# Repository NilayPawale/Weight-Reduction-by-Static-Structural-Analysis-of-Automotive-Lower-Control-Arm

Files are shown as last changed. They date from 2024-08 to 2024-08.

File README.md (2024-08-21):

# Weight-Reduction-by-Static-Structural-Analysis-of-Automotive-Lower-Control-Arm

The control arm is a unique type of independent suspension used in automobile vehicles. 
During the actual working condition, the maximum load is transferred from upper arm to 
the A arm which creates possibility of failure in the arm. Hence it is essential to focus on 
the stress analysis of A control arm to improve and modify the existing design. A control 
arm is an important part used in a suspension system of a car. control arm performance a 
major role in managing the motion of the wheel during bump, turning, and breaking. This 
paper proposed the design optimization and model analysis of steel cast for the front A 
control arm was investigated. CATIA software was utilized to design the A control arm. 
ANSYS 19 software was also used to analyze the structural strength and optimize the parts 
weight. The target of the new design was a 20% weight reduction from the existing part 
fabricated using steel material. Testing and validation of new design using FFT analysis. 
Model analysis carried out to find out natural frequencies of A control arm and validation 
are done with the help of FFT analyzer and Impact Hammer Test. 

The lower control arm gets more attention by many researches like study dynamic analyses 
of the motor vehicle suspension system using the point-joint coordinate’s formulation. The 
mechanical system is replaced by an equivalent constrained system of particles and then 
the laws of particle dynamics are used to derive the equations of motion. Modelling and 
simulation are indispensable when dealing with complex engineering systems. It makes it 
possible to do an essential assessment before systems are developed. It can provide support 
in all stages of a project from conceptual design, through commissioning and operation. 
The most effective was to improve product quality and reliability is to integrate them in 
the design and manufacturing process. 

## Significance of Project 

The suspension system caries the vehicle body and transmit all forces between the body 
and the road without transmitting to the driver and passengers. The suspension system of a 
car is used to support its weight during varying road conditions. The suspension system is 
made of several parts and components. These include the front and rear. The suspension 
arm gets more attention by many researches like study dynamic analyses of the motor 
vehicle suspension system using the point-joint coordinate’s formulation. Modeling and 
simulation are indispensable when dealing with complex engineering systems. It can 
provide support in all stages of a project from conceptual design, through commissioning 
and operation. The most effective way to improve product quality and reliability is to 
integrate them in the design and manufacturing process. 

## Objectives

1. To prepare CAD design using CATIA V5. 
2. Static structural Analysis of Automotive A type control arm 
3. Optimization of Automotive A type control arm. 
4. To perform static structural analysis of the suspension arm using ANSYS Software. 
5. To optimize the lower control arm for weight reduction” (unsprung weight) up to 
5-20% and suggest alternate design. 
6. Testing and validation of Automotive A type control arm with the help of 
Universal Testing Machine. 
7. To compare the factor of safety for optimized and baseline design of lower 
control arm by keeping factor of safety for optimized design within permissible 
limits. 
8. To perform experimentation on physical model of Lower Control Arm.

## Softwares Used: 
Catia, SolidWorks, Ansys

## Results obtained from the project

### Elements Details of Ansys -  
- Nodes – 28547 for Existing component and 27382 for Optimized component. 
- Elements - 14197 for Existing component and 13451 for Optimized component. 

### Universal Testing Machine Results -  
- The Deformation Maximum is 2.593mm for Existing component and 2.869 mm 
for Optimized component. 
- The Deformation Minimum is 0mm for Existing component and 0mm for 
Optimized component. 
- The Von-mises stress Maximum are 350.22 MPA for Existing component and 
399 MPA for Optimized component. 
- The Von-mises stress Minimum are 0.0012 MPa for Existing component and 
0.0014 MPA for Optimized component. 
- Mass of the Existing component is 2.55 KG for Existing component and 2.39 KG 
(6.07% weight reduction) for Optimized component. 
- Factor of Safety of the Existing component is 1.31 for existing component and 
1.15 for Optimized component. 

The existing design has been modified, by reducing the thickness of the existing profile. 
The optimization of lower control arm is done by applying the Design of Experiments 
method. The parameters are identified. The FEA is done on LCA and the buckling load 
has been compared with the existing component. The sheet metal thickness of the new 
design has been reduced from 3.6 mm to 3mm. For the mass production the cost has been 
reduced to Rs.34000 for 2000 products in a batch as assumed. For the modified design 
the structural rigidity has been increased for the LCA, when compared to the existing 
design. Finally, mass of the control arm has been reduced up to 6.07 % when compared 
with existing model.

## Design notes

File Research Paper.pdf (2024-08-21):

# Weight Reduction by Static Structural Analysis of Automotive Lower Control Arm

Aniruddha Jadhav#1, Nilay Pawale *2, Atharva Kalokhe #3

### , Aditya Bangale #4

#Department of Mechanical Engineering, Smt Kashibai Navale College of Engineering, Savitribai Phule Pune University, Pune 1Aniruddhaj7727@gmail.com

2nilaypawale.skncoe.mech@gmail.com 3atharvkalokhe05@gmail.com 4bangale.adi@gmail.com
Abstract—
The lower control arm is a unique type of independent suspension used in automobile vehicles. During the actual working condition, the maximum load is transferred from upper arm to the A arm which creates possibility of failure in the arm. Hence it is essential to focus on the stress analysis of A suspension arm to improve and modify the existing design. A suspension arm is an important part used in a suspension system of a car. suspension arm performance a major role in managing the motion of the wheel during bump, turning, and breaking. This research proposed the design optimization and static analysis of steel cast for the front A suspension arm was investigated. CATIA software was utilized to design the A suspension arm. ANSYS 19 software was also used for analyze the structural strength and optimize the parts weight. The target of the new design was a 20% weight reduction from the existing part fabricated using steel material. Testing and validation of new design using strain gauge analysis.
Keywords— Lower Control Arm, Suspension System, Weight Reduction, Ansys, Catia
I. INTRODUCTION

The control arm is a unique type of independent suspension used in automobile vehicles. During the actual working condition, the maximum load is transferred from upper arm to the A arm which creates possibility of failure in the arm. Hence it is essential to focus on the stress analysis of A control arm to improve and modify the existing design. A control arm is an important part used in a suspension system of a car. control arm performance a major role in managing the motion of the wheel during bump, turning, and breaking. This paper proposed the design optimization and model analysis of steel cast for the front A control arm was investigated. CATIA software was utilized to design the A control arm. ANSYS 19 software was also used to analyse the structural strength and optimize the parts weight. The target of the new design was a 20% weight reduction from the existing part fabricated using steel material.
In automotive suspension, a control arm, also known as an A-arm, is a hinged suspension link between the chassis and the suspension upright or hub that carries the wheel. In simple terms, it governs a wheel's vertical travel, allowing it to move up or down when driving over bumps, into potholes, or otherwise reacting to the irregularities of a road surface. Most control arms form the lower link of a suspension.

The challenge for automotive manufacturer to produce the lightweight components but at the same time need to maintain the performance of the components. To produce the lightweight components, the main criteria to overlook are the advance material and the manufacturing technology.
Weight reduction enables the manufacturer to develop the same vehicle. If all the components in vehicle can contributed for about 10% to 20% of weight reduction, it is estimated that 20% of vehicle weight reduction results in 8–10% of fuel economy improvement. There several ways to achieve the lightweight components in vehicle. Changing a new lightweight material such as composites and aluminium alloy can give a good weight reduction to vehicle and improve the fuel economy [1].

II. LITERATURE REVIEW

Vehicles ranging from bullock carts to modern vehicles use suspension system such as, leaf springs, pneumatic and hydraulic systems. The main aim of using a suspension system is to prevent the shocks reaching the body of the vehicle from the rough roads and ensure that the vehicle’s wheels remain in contact with the road. There are two types of forces acting on the suspension system of a vehicle, the first is the force from the road disturbance, and the second is the load disturbance. Road unevenness could be of high magnitude and low frequency (such as mountains) and the small magnitude and large frequency (because of rough roads). Load disturbance includes the forces induced by the changing acceleration, braking and cornering. A suspension system should respond very smoothly against road disturbances and should be robust against load disturbances.[2]
In suspension system, the control arm is very important component. The double wishbone suspension system contains lower control arm and upper control arm. The McPherson structural suspension system contains only lower control arm. Between wheel assembly and vehicle chassis the control arms are rigidly placed.
The control arm is connected to the chassis with the help of bush which is placed in pivot joints. Rear and front bushes are used in control arms. it has U-shaped configuration. At the apex of the control arm a ball joint receptacle is formed.[3]

The ball joint receptacle is adapted to cooperate with a ball joint assembly and may include a ball joint housing integrally formed with the control arm. Typical modern control arm incorporates a separate ball joint housing which is inserted in to the apex of control arm. The bushing apertures are designed to retain pipe housings for mating engagement with a pivot bar assembly forming a portion of the vehicle suspension system.[3]

III. PROBLEM DEFINITION AND OBJECTIVES

Chassis parts are a critical part of a vehicle, leaving no room for error in the design and quality the present process relates to a computer-aided structure analysis and design graphic display device and method, and more particularly, to a computer-aided structure analysis of A control arm and which is analyzed and designed, thereby meet the customer requirements of LCA.

Objectives:
1. To prepare CAD design using CATIA V5.

### 2. Static structural Analysis of Automotive A type control arm

3. Optimization of Automotive A type control arm.
4. To perform static structural analysis of the suspension arm using ANSYS Software.
5. To optimize the lower control arm for weight reduction” (unsprung weight) up to 5-20% and suggest alternate design.
6. To compare the factor of safety for optimized and baseline design of lower control arm by keeping factor of safety for optimized design within permissible limits.
7. To perform experimentation on physical model of Lower Control Arm.

IV.METHODOLOGY
The methodology of our project would be starting with the topic selection, then working on the topic by researching and creating a detailed plan for execution of the project. Then executing the project by manufacturing and then testing the model of the project. Then at last finishing the miscellaneous work and concluding the Project.

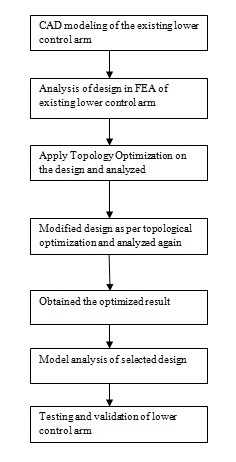
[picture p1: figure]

V. DESIGN OF LOWER CONTROL ARM

The finite element method (FEM), is a numerical method for solving problems of engineering and mathematical physics. Typical problem areas of interest include structural analysis, heat transfer, fluid flow, mass transport, and electromagnetic potential. The analytical solution of these problems generally requires the solution to boundary value problems for partial differential equations. The finite element method formulation of the problem results in a system of algebraic equations. The method yields approximate values of the unknowns at discrete number of points over the domain. To solve the problem, it subdivides a large problem into smaller, simpler parts that are called finite elements.

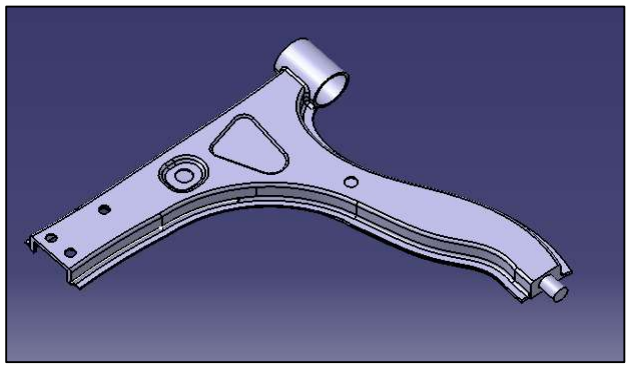
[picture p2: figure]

Lower Control Arm CAD

In present research for analysis ANSYS (Analysis System) software is used. Basically, its present FEM method to solve any problem. Following are steps in detail

### 1. Geometry 2. Discretization (Meshing) 3. Boundary condition 4. Solve (Solution) 5. Interpretation of results

Step 1: Details of material namely copper, steel, grey cast iron, composite material, fluid domain material is defined in engineering data. i.e., ANSYS default material is structural steel.
Step 2: Import of geometry created in any CAD software namely CATIA, PRO E, SOLIDWORK, INVENTOR etc. in geometry section. If any correction is to be made it can be created in geometry section in Design modeller or space claim.
Step 3: In model section after import of component
- Material is assigned to component as per existing material
- Connection is checked in contact region i.e., bonded, frictionless, frictional, no separation etc. for multi body components.
- Meshing or discretization is performed i.e., to break components in small pieces (elements) as per size i.e., preferably tetra mesh and hexahedral mesh for 3D geometry and for 2 D quad or trial are generally preferred.
Step 4: Boundary condition are applied as per analysis namely in fixed support, pressure, force, displacement, velocity as per condition.
Step 5: Now problem is well defined and solve option is selected to obtain the solution in the form of equivalent stress, strain, energy, reaction force etc.
Table 1. Material properties

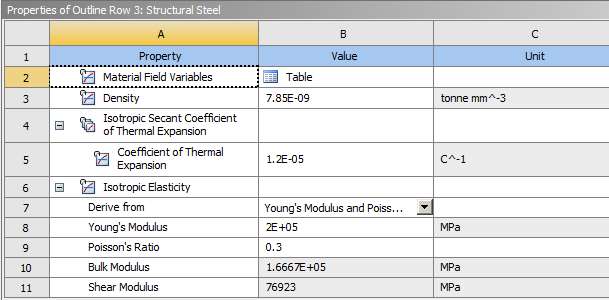
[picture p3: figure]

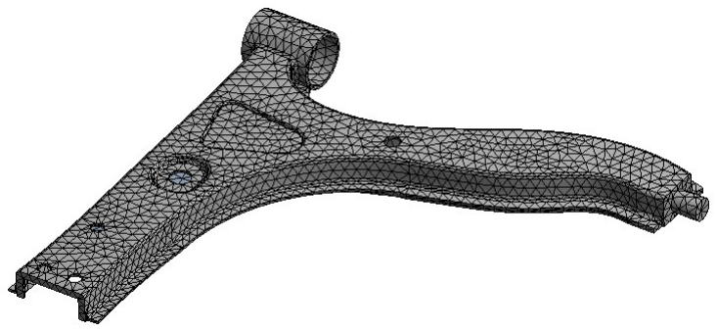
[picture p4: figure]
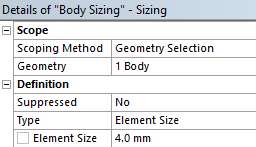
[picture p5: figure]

Fig 1. Meshing of model

Fig 2. Elements Details

A. Boundary Condition

A boundary condition for the model is the setting of a known value for a displacement or an associated load. For a particular node you can set either the load or the displacement but not both.
The main types of loading available in FEA include force, pressure and temperature. These can be applied to points, surfaces, edges, nodes and elements or remotely offset from a feature. The way that the model is constrained can significantly affect the results and requires special consideration. Over or under constrained models can give stress that is so inaccurate that it is worthless to the engineer. In an ideal world we could have massive assemblies of components all connected to each other with contact elements but this is beyond the budget and resource of most people. We can however, use the computing hardware we have available to its full potential and this means understanding how to apply realistic boundary conditions.

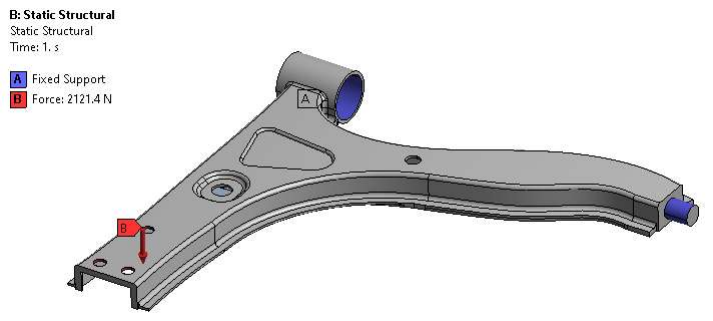
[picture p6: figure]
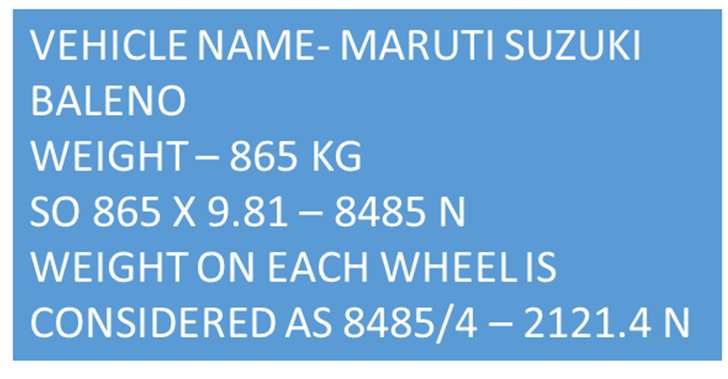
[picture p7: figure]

Fig 3. Boundary condition of model

B. Total Deformation

The total deformation & directional deformation are general terms in finite element methods irrespective of software being used. Directional deformation can be put as the displacement of the system in a particular axis or user defined direction. Total deformation is the vectors sum all directional displacements of the systems.

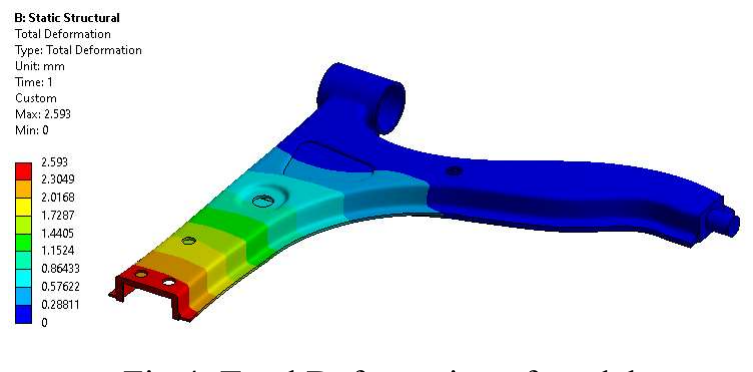
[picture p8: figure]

Fig 4. Total Deformation of model

C. Steps in Topology Optimization

The topology optimization consists of the following sequence of steps.
- Define the design space
- Define optimization parameters
- Material removal process and detail design
Step 1: Details of material namely copper, steel, grey cast iron, composite material, fluid domain material is defined in engineering data. i.e., ANSYS default material is structural steel.
Step 2: Import of geometry created in any CAD software namely CATIA, PRO E, SOLIDWORK, INVENTOR etc. in geometry section. If any correction is to be made it can be created in geometry section in Design modeller or space claim.
Step 3: In model section after import of component
- Material is assigned to component as per existing material
- Connection is checked in contact region i.e., bonded, frictionless, frictional, no separation etc. for multi body components.
- Meshing or discretization is performed i.e., to break components in small pieces (elements) as per size i.e., preferably tetra mesh and hexahedral mesh for 3D geometry and for 2 D quad or trial are generally preferred.
Step 4: Boundary condition are applied as per analysis namely in fixed support, pressure, force, displacement, velocity as per condition.
Step 5: Now problem is well defined and solve option is selected to obtain the solution in the form of equivalent stress, strain, energy, reaction force etc.
Step 6: Topology optimization tool is selected from ANSYS list view and drag and dropped in solution section of static structural so that it takes its all-boundary condition, geometry, all details and perform topology optimization on selected component.
Step 7: Define the topology density and element density section as output. After performing topology algorithm on component, selected parts contain red, brown and grey colour on it. So, red region colour indicates material removal area along with marginal (brown colour) and grey colour to keep material.
Step 8: After selection of specific shape material is removed from component and reanalysis of component is performed to observe the sustainability of existing optimized component under same boundary condition.

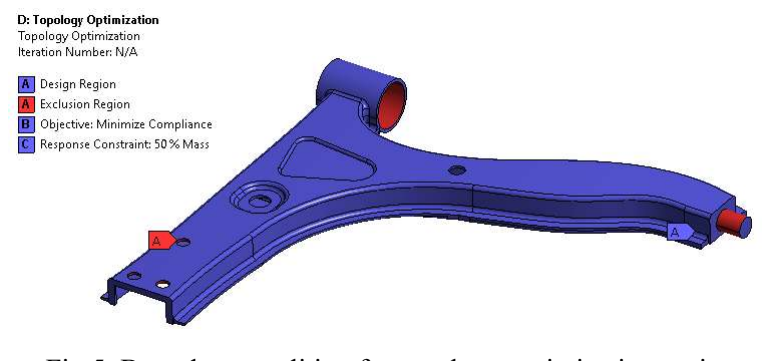
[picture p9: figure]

Fig 5. Boundary condition for topology optimization region

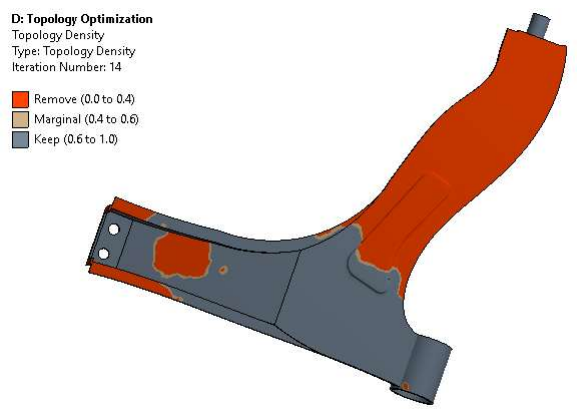
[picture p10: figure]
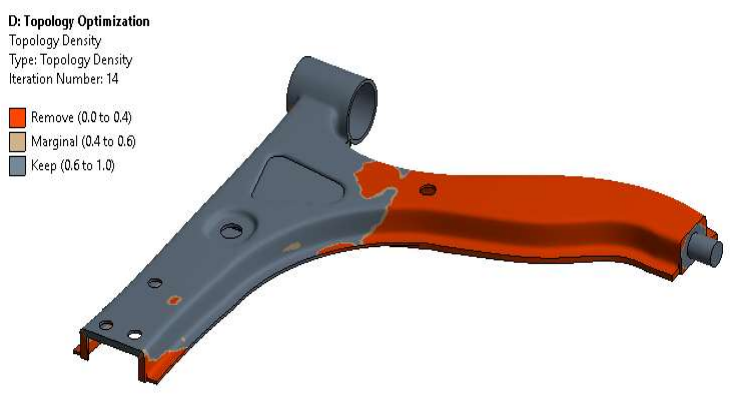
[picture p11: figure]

Fig 6. Topology optimized results

- Red region indicates material removal area region.

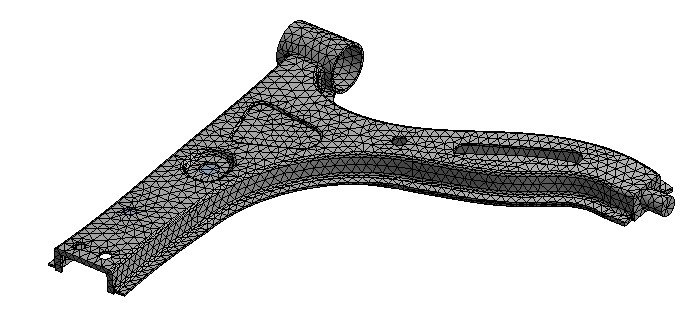
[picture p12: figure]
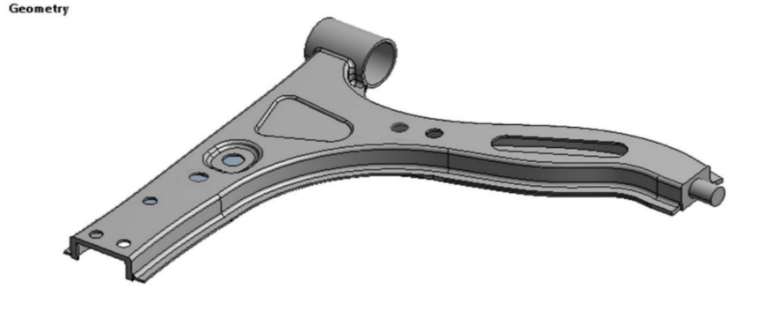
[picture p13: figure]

Fig 7. Optimized lower control arm

Fig 8. Details of optimized lower control arm

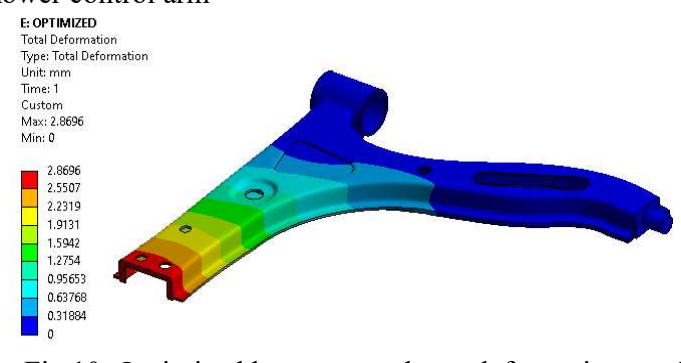
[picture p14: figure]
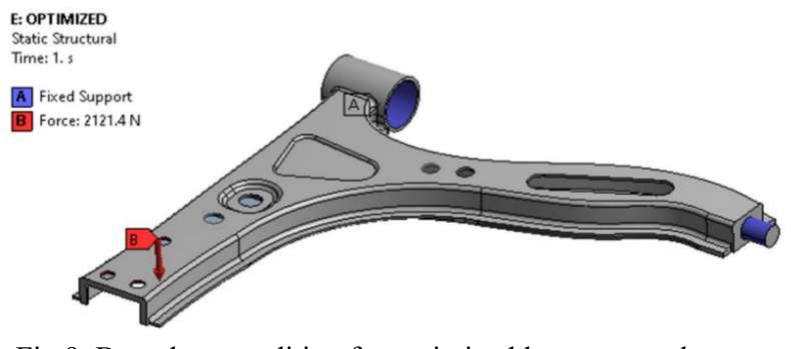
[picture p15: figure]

Fig 9. Boundary condition for optimized lower control arm | Fig 10. Optimized lower control arm deformation result

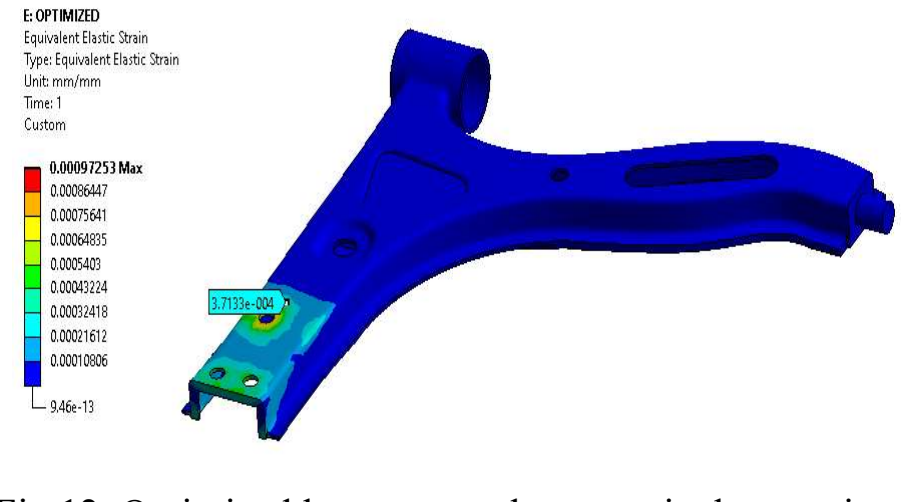
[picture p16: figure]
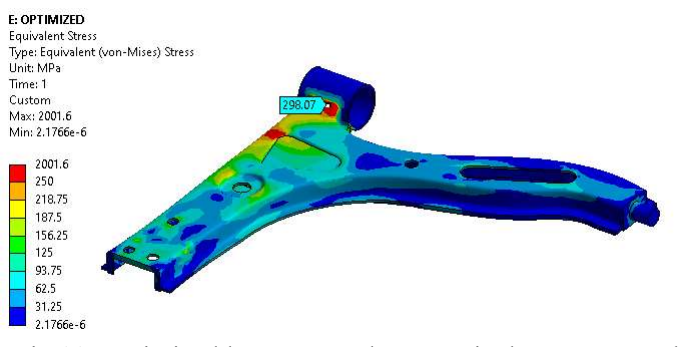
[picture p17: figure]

Fig 11. Optimized lower control arm equivalent stress result | Fig 12. Optimized lower control arm equivalent strain result
- Strain is observed around 371 microns.

VI.EXPERIMENTAL TEST

A Universal Testing Machine (UTM) is used to test both the tensile and compressive strength of materials. Universal Testing Machines are named as such because they can perform many different varieties of tests on an equally diverse range of materials, components, and structures.
Universal Testing Machines can accommodate many kinds of materials, ranging from hard samples, such as metals and concrete, to flexible samples, such as rubber and textiles. This diversity makes the Universal Testing Machine equally applicable to virtually any manufacturing industry.

TABLE 2 -SPECIFICATION OF UTM

1 | Max Capacity | 400KN
2 | Measuring range | 0-400KN
3 | Least Count | 0.04KN
4 | Clearance for Tensile Test | 50-700 mm
5 | Clearance for Compression Test | 0- 700 mm
6 | Clearance Between column | 500 mm
7 | Ram stroke | 200 mm
8 | Power supply | 3 Phase, 440Volts, 50 cycle. A.C
9 Overall dimension of machine | (L*W*H) | 2100*800*2060
10 | Weight | 2300Kg

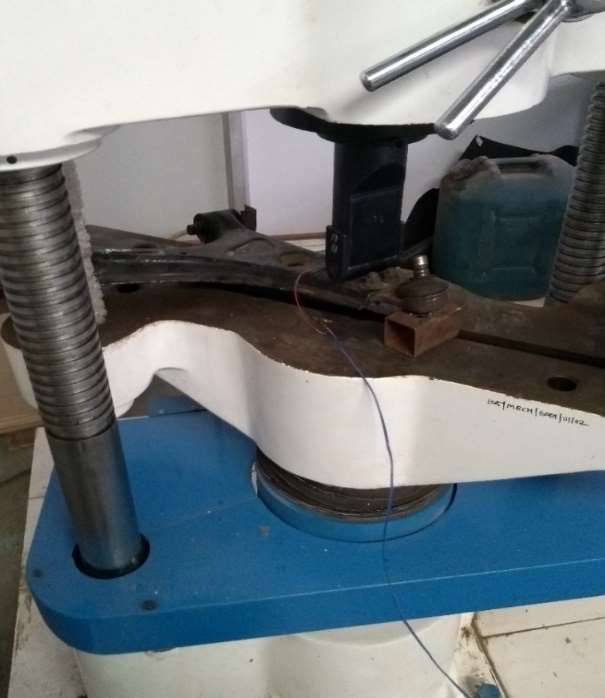
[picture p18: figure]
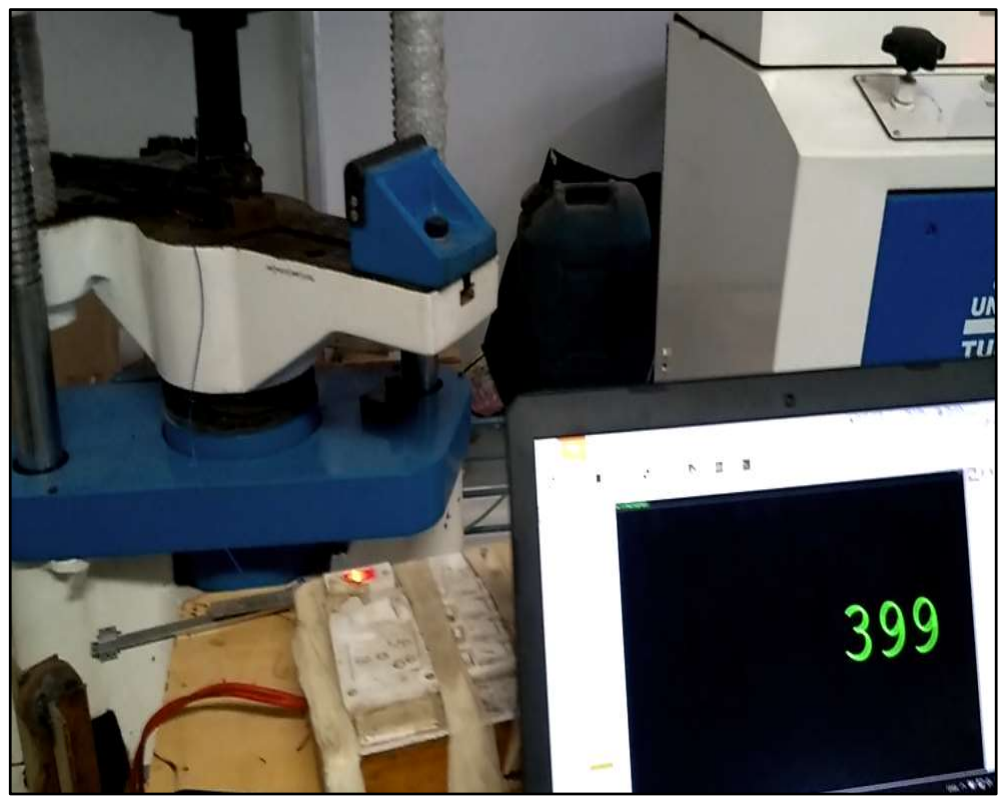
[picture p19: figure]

Fig 13. Testing in Universal Testing Machine | Fig 14. Experimental testing results

TABLE 3 - Evaluation of Results

S. No | Parameters | Existing component | Optimized component
d1 | Deformation (mm) | Max | 2.593mm | 2.869 mm
| | Min | 0 mm | 0 mm
2 Von-mises stress | (Mpa) | Max | 350.22 Mpa | 399 Mpa
| | Min | 0.0012 MPa | 0.0014 MPa
3 | Mass reduction | | 2.55 | 2.39 | 6.07% weight reduction
4 | Factor of Safety | 1.31 | | 1.15

VII. SCOPE OF FUTURE WORK

This project can be extended to satisfy the following requirements as the key objectives:
- Implementing new design changes in the existing model can be done
- Identifying more materials for the proposed design and new design
- Increasing the number of levels of the response
- Based on observations design improvements will be made in terms of shape, size and material based on design modification objectives.
- The study will focus on existing design performance, advantage and limitations.

VIII.CONCLUSION

As deflection and stress of modified Lower Control Arm is within the range. Thus, the modified design is safe. Weight of the final optimized model is 2.39 kg. The total reduction in mass is observed 6.07% by keeping Factor of safety for optimized design within permissible limits.
Thus, the objective of weight reduction of unsprung mass and cost reduction has been achieved.

ACKNOWLEDGEMENT

We take this opportunity to thank all those who have contributed to successful completion of this research work. We
would like to express our sincere thanks to our guide Prof. R. N. Khachane who has encouraged us to work on this topic and also provided valuable guidance wherever required. We also extend our gratitude to Prof. T. S. Sargar (H.O.D
Mechanical Department) who have provided facilities to explore the subject with more enthusiasm.
We express our immense pleasure and thankfulness to all the teachers and staff of the Department of Mechanical Engineering of Shrimati Kashibai Navale College of Engineering for their co-operation and support.

REFERENCES

[1] Introduction of Design and Optimization of Front Lower Control Arm (FLCA) for C-Segment Passenger Car Mohd Hafizi Abdul Rahman, Mohd Shukor Salleh, Mohd Suffian Ab. Razak, Mohamad Ridzuan Mohamad Kamal, Zolkarnain Marjom, Liza Anuar and Nur Adzly Mohamad Saad
[2] Design and analysis of lower control arm of suspension system, M. Sadiq A. Pachapuri, Ravi G. Lingannavar, Nagaraj K. Kelageri, Kritesh K. Phadate Department of Mechanical Engineering, KLE Dr. M. S. Sheshgiri College of Engineering and Technology, Belagavi 590008, India
[3] COMPARISION STUDY OF LOWER CONTROL ARM WITH DIFFERENT MATERIAL, by Gururaj Dhanu and Prof. R.S.Kattimani M.Tech (Machine Design), B.L.D.E. A’s V. P. Dr.P.G.H College of Engineering and Technology, Vijayapur, Karnataka, India, Professor, Dept. of Mechanical Engineering, B.L.D.E. A’s V. P. Dr.P.G.H College of Engineering and Tehnology, Vijayapur, Karnataka, India
[4] Structural optimization of control arm for weight reduction and improved performance by Mohd Viqaruddina, D.Ramana Reddy

[5] Design and Optimization of Front Lower Control Arm (FLCA) for C-Segment Passenger Car Mohd Hafizi Abdul Rahman, Mohd Shukor Salleh, Mohd Suffian Ab. Razak, Mohamad Ridzuan Mohamad Kamal, Zolkarnain Marjom, Liza Anuar and Nur Adzly Mohamad Saad
[6] A new design optimization of light weight front lower control arm, M.H.A. Rahman, M.S. Salleh, A. Abdullah, S.H. Yahaya, M.S.A. Razak, M.R.M. Kamal, Z. Marjom, L. Anuar and N.A.M. Saad, Journal of Advanced Manufacturing Technology (JAMT), ISSN: 1985-3157 Vol. 12 No. 1 January - June 2018.
[7] Analysis and Optimization of Lower Control Arm, Kale AR, Tadamalle AP and Patil ND, crimnson publishers, evolution in mechanical engineering, ISSN: 2640-9690, August 07, 2018
[8] Design Optimization of a Lower Control Arm of Suspension System in a LCV by using Topological Approach, Swapnil S. Khode, Prof. Amol N. Patil, Prof. Amol B. Gaikwad, International Journal of Innovative Research in Science, Engineering and Technology Vol. 6, Issue 6, June 2017
[9] Optimization of the lower arm of a vehicle suspension system for road noise reduction by sensitivity analysis, Yong-Dae Kim, Jae-Eun Jeong , Jin-Su Park , In-Hyung Yang , Tae-Sang Park , Pauziah Binti Muhamad , Dong-Hoon Choi , Jae-Eung Oh, Mechanism and Machine Theory 69 (2013) 278–302
[10] Topology Optimization and Performance Calculation for Control Arms of a Suspension Liang Tang, JieWu, Jinhao Liu, Cuicui Jiang, andWen-Bin Shangguan, Hindawi Publishing Corporation Advances in Mechanical Engineering, Volume 2014, Article ID 734568

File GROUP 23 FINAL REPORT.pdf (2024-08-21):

Savitribai Phule Pune University, Pune 2019 Course

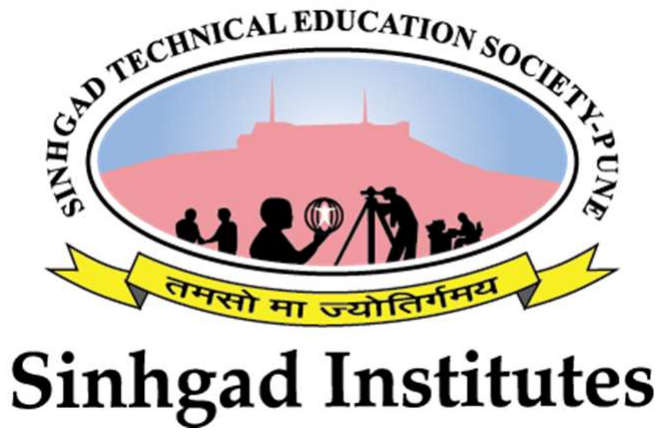
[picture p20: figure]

Smt. Kashibai Navale College of Engineering, Pune | B.E. (Mechanical Engineering)

### A Project Stage-II Report on

# Weight Reduction by Static Structural Analysis of Automotive Lower Control Arm

By

Mr. Aniruddha Jadhav | Exam. Seat No – B190360969
Mr. Nilay Pawale | Exam. Seat No – B190361088
Mr. Atharva Kalokhe | Exam. Seat No – B190360992
Mr. Aditya Bangale | Exam. Seat No – B190360828

### Guide Prof. R.N. Khachane

## Department of Mechanical Engineering

### Sinhgad Technical Education Society’s

## Smt. Kashibai Navale College of Engineering

[2022-23]

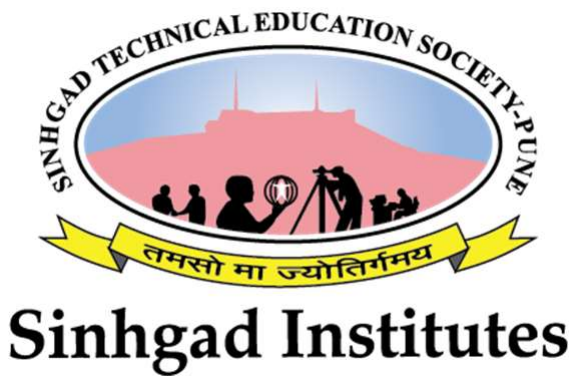
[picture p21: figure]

Smt. Kashibai Navale College of Engineering, Pune | B.E. (Mechanical Engineering)

## Sinhgad Technical Education Society’s Smt. Kashibai Navale College of Engineering

## C E R T I F I C A T E

This is to certify that Mr. Aniruddha Jadhav Exam. Seat No – B190360969
Mr. Nilay Pawale | Exam. Seat No – B190361088
Mr. Atharva Kalokhe | Exam. Seat No – B190360992
Mr. Aditya Bangale | Exam. Seat No – B190360828
have successfully completed the Project Stage – II entitled “Weight Reduction by Static Structural Analysis of Automotive Lower Control Arm” under my supervision, in the partial fulfillment of Bachelor of Engineering - Mechanical Engineering of Savitribai Phule Pune University.

Date: -
Place: - Pune

Prof. R.N. Khachane
Guide
Prof |
External Examiner

Prof. T. S. Sargar
Head of Department

Dr. A.V. Deshpande
Principal

### Seal

Smt. Kashibai Navale College of Engineering, Pune | B.E. (Mechanical Engineering)

### ACKNOWLEDGEMENT

I take this opportunity to thank all those who have contributed in successful completion of this Project Stage -II work. I would like to express my sincere thanks to my guide Prof. R.N. Khachane who have encouraged me to work on this topic and provided valuable guidance wherever required. I also extend my gratitude to Prof. T. S. Sargar (H.O.D Mechanical Department) who has provided facilities to explore the subject with more enthusiasm.

I express my immense pleasure and thankfulness to all the teachers and staff of the Department of Mechanical Engineering of Smt. Kashibai Navale College of Engineering for their co-operation and support.

Mr. Aniruddha Jadhav Sign. |
Mr. Nilay Pawale | Sign. |
Mr. Atharva Kalokhe | Sign. |
Mr. Aditya Bangale | Sign. |

Smt. Kashibai Navale College of Engineering, Pune | B.E. (Mechanical Engineering)

### Abstract

The lower control arm is a unique type of independent suspension used in automobile vehicles. During the actual working condition, the maximum load is transferred from upper arm to the A arm which creates possibility of failure in the arm. Hence it is essential to focus on the stress analysis of A suspension arm to improve and modify the existing design. A suspension arm is an important part used in a suspension system of a car. suspension arm performance a major role in managing the motion of the wheel during bump, turning, and breaking. This research proposed the design optimization and static analysis of steel cast for the front A suspension arm was investigated. CATIA software was utilized to design the A suspension arm. ANSYS 19 software was also used for analyze the structural strength and optimize the parts weight. The target of the new design was a 20% weight reduction from the existing part fabricated using steel material. Testing and validation of new design using strain gauge analysis.

Smt. Kashibai Navale College of Engineering, Pune | B.E. (Mechanical Engineering)

TABLE OF CONTENTS

SR. NO. | CONTENTS | PAGE NO.
1 | CHAPTER 1: INTRODUCTION | 1
| 1.1 Topic | 1
| 1.2 Background of the Project | 2
| 1.3 – Significance of Project | 5
2 | CHAPTER 2: LITERATURE SURVEY | 6
3 | CHAPTER 3: PROBLEM DEFINITION AND OBJECTIVES | 21
| 3.1 PROBLEM DEFINITION | 21
| 3.2 OBJECTIVES | 21
4 | CHAPTER 4: METHEDOLOGY | 22
5 CHAPTER 5: DESIGN, ANALYSIS AND DESIGN | OPTIMIZATION | 24
| 5.1 FEA (Finite Element Analysis) | 24
| 5.2 Boundary Condition | 29
| 5.3 Experimental Test | 37
6 | CHAPTER 6: RESULTS AND DISCUSSION | 40
7 | CHAPTER 7: CONCLUSION | 41
| REFERENCES AND BIBLIOGRAPHY | 42
| PHOTOGRAPH OF LOWER CONTROL ARM MODEL | 45
| WEEKLY WORK FLOW | 46

Smt. Kashibai Navale College of Engineering, Pune | B.E. (Mechanical Engineering)

LIST OF TABLES AND FIGURES

List of Tables

SR. NO. | TABLE NAME | PAGE NO.
1 | Table 1 - Flowchart for the Methodology | 23
2 | Table 2 - Table of Material properties | 28
3 | Table 3 - Meshing of model | 29
4 | Table 4 - Elements Details | 29
5 | Table 5 - Details of optimized lower control arm | 34
6 | Table 6 – Specification of Universal Testing Machine | 38
7 | Table 7 -Evaluation of Results | 39
8 | Weekly Work Flow | 46

Smt. Kashibai Navale College of Engineering, Pune | B.E. (Mechanical Engineering)

List of Figures

SR. NO. | FIGURE NAME | PAGE NO.
1 | Figure 1.1 – Automobile Lower Control Arm | 1
2 | Figure 1.2 – Dependent and Independent Suspension | 4
3 | Figure 1.3 – Automobile Lower Control Arm Location | 5
4 | Fig. 5.1 - CATIA model | 25
5 | Fig.5.2 - Drafting of existing model | 25
6 | Fig.5.3 – Complete Model Assembly | 26
7 | Fig.5.4 – Ball Joint CAD | 26
8 | Fig.5.5 – Ball Joint CAD | 26
9 | Fig.5.3 - Existing design of lower control arm | 28
10 | Fig.5.4 - Meshing of model | 29
11 | Fig.5.5 - Boundary condition of model | 30
12 | Fig.5.6 - Total Deformation of model | 31

Smt. Kashibai Navale College of Engineering, Pune | B.E. (Mechanical Engineering)
13 | Fig.5.7 - Boundary condition for topology optimization region | 32
14 | Fig.5.8 - Topology optimized results | 33
15 | Fig.5.9 - Topology optimized results | 33
16 | Fig.5.10 - Optimized lower control arm | 34
17 | Fig.5.11 - Details of optimized lower control arm | 34
18 | Fig.5.12 - Boundary condition for optimized lower control arm | 35
19 | Fig.5.13 - Optimized lower control arm deformation result | 35
20 | Fig.5.14 - Optimized lower control arm equivalent stress result | 36
21 | Fig.5.15 - Optimized lower control arm equivalent strain result | 36
22 | Fig.5.16 - Testing in Universal Testing Machine | 38
23 | Fig.5.17 - Experimental testing results | 39
24 | Photograph of Lower Control Arm Model | 45

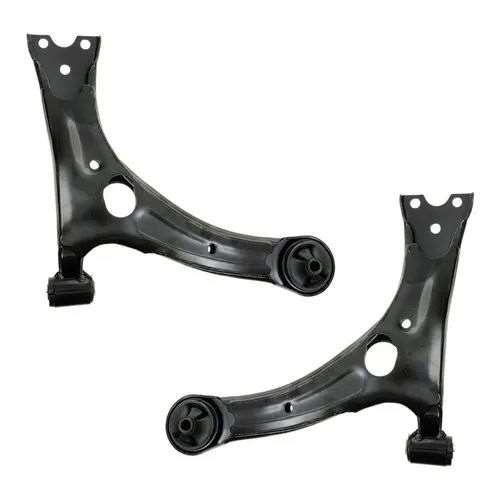
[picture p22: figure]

Smt. Kashibai Navale College of Engineering, Pune | B.E. (Mechanical Engineering)
1

### CHAPTER 1: INTRODUCTION

1.1 - Introduction
The control arm is a unique type of independent suspension used in automobile vehicles. During the actual working condition, the maximum load is transferred from upper arm to the A arm which creates possibility of failure in the arm. Hence it is essential to focus on the stress analysis of A control arm to improve and modify the existing design. A control arm is an important part used in a suspension system of a car. control arm performance a major role in managing the motion of the wheel during bump, turning, and breaking. This paper proposed the design optimization and model analysis of steel cast for the front A control arm was investigated. CATIA software was utilized to design the A control arm. ANSYS 19 software was also used to analyze the structural strength and optimize the parts weight. The target of the new design was a 20% weight reduction from the existing part fabricated using steel material. Testing and validation of new design using FFT analysis. Model analysis carried out to find out natural frequencies of A control arm and validation are done with the help of FFT analyzer and Impact Hammer Test.

Figure 1.1 – Automobile Lower Control Arm

Smt. Kashibai Navale College of Engineering, Pune | B.E. (Mechanical Engineering)
2

1.2 - Background of the Project

The lower control arm gets more attention by many researches like study dynamic analyses of the motor vehicle suspension system using the point-joint coordinate’s formulation. The mechanical system is replaced by an equivalent constrained system of particles and then the laws of particle dynamics are used to derive the equations of motion. Modelling and simulation are indispensable when dealing with complex engineering systems. It makes it possible to do an essential assessment before systems are developed. It can provide support in all stages of a project from conceptual design, through commissioning and operation. The most effective was to improve product quality and reliability is to integrate them in the design and manufacturing process.

The challenge for automotive manufacturer to produce the lightweight components but at the same time need to maintain the performance of the components. To produce the lightweight components, the main criteria to overlook are the advance material and the manufacturing technology.
Weight reduction enables the manufacturer to develop the same vehicle. If all the components in vehicle can contributed for about 10% to 20% of weight reduction, it is estimated that 20% of vehicle weight reduction results in 8–10% of fuel economy improvement. There several ways to achieve the lightweight components in vehicle. Changing a new lightweight material such as composites and aluminum alloy can give a good weight reduction to vehicle and improve the fuel economy [1].

Nowadays, several automotive manufacturers already change from steel alloy and cast iron to alternative lightweight material such as composite and aluminum alloy. The market pattern for material shows gradual decrease for steel and cast-iron usage in automotive industries. [1].

Ford as one of the automotive manufacturers widely used the aluminum alloy in body in white structure and closure such as panel door outer, roof, panel hood outer, trunk lid,

Smt. Kashibai Navale College of Engineering, Pune | B.E. (Mechanical Engineering)
3

tailgate, etc. For examples, Ford F150 model 2015 mostly used Aluminum alloy for the body in white structures and at the closure panels. Meanwhile, the Cadillac ATS and CT6 used mixing material such as using aluminum casting, high strength steels and sheet metals on their BIW and closures panels [1].

1.3 - Lower Control Arm

In automotive suspension, a control arm, also known as an A-arm, is a hinged suspension link between the chassis and the suspension upright or hub that carries the wheel. In simple terms, it governs a wheel's vertical travel, allowing it to move up or down when driving over bumps, into potholes, or otherwise reacting to the irregularities of a road surface. Most control arms form the lower link of a suspension. Control arms play a crucial role in the suspension system of a vehicle. They help to keep the wheels aligned and maintain proper tire contact with the road, which is essential for safety and stability.

Dependent suspension system:

A dependent suspension normally has a beam (a simple 'cart' axle) or (driven) live axle that holds wheels parallel to each other and perpendicular to the axle. When the camber of one-wheel changes, the camber of the opposite wheel changes in the same way (by convention on one side this is a positive change in camber and on the other side this a negative change). De Dion suspensions are also in this category as they rigidly connect the wheels together. Example: Hotchkiss suspension and trailing arm suspension comes under this Category.

Independent suspension system:

An independent suspension allows wheels to rise and fall on their own without affecting the opposite wheel. In this case, the wheels are connected through universal joints with a swing axle. Suspensions with other devices, such as sway bars that link the wheels in some ways are still classed as independent. Example: The two important types of independent systems are Macpherson strut and Double wishbone system.

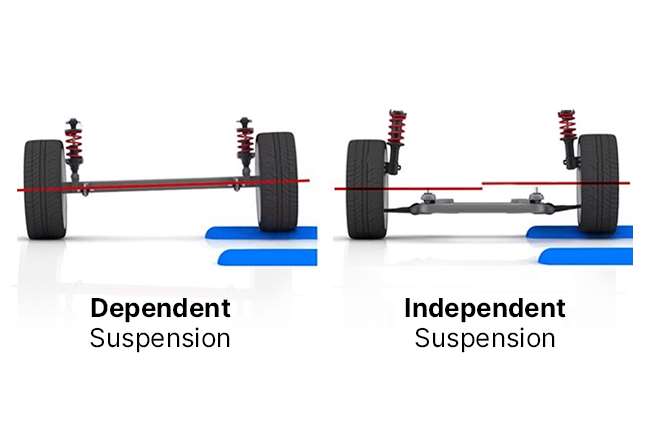
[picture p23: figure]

Smt. Kashibai Navale College of Engineering, Pune | B.E. (Mechanical Engineering)
4

Figure 1.2 – Dependent and Independent Suspension

Lower Control Arm:

The lower control arm is the most vital component in a suspension system. There are two control arms, lower control arm and upper control arm. Lower control arm allows the up and down motion of the wheel. It is usually a steel bracket that pivots on rubber bushings mounted to the chassis.

The other end supports the lower ball joint. Significant number of loads are transmitted through the control arm while it serves to maintain the contact between the wheel and the road and thus providing the precise control of the vehicle. There are many types of control arms are available. The selection of the arm is mainly based on the type of suspension system.

In automotive suspension, a control arm, also known as an A-arm, is a hinged suspension link between the chassis and the suspension upright or hub that carries the wheel. In simple terms, it governs a wheel's vertical travel, allowing it to move up or down when driving over bumps, into potholes, or otherwise reacting to the irregularities of a road surface. Most control arms form the lower link of a suspension. [1].

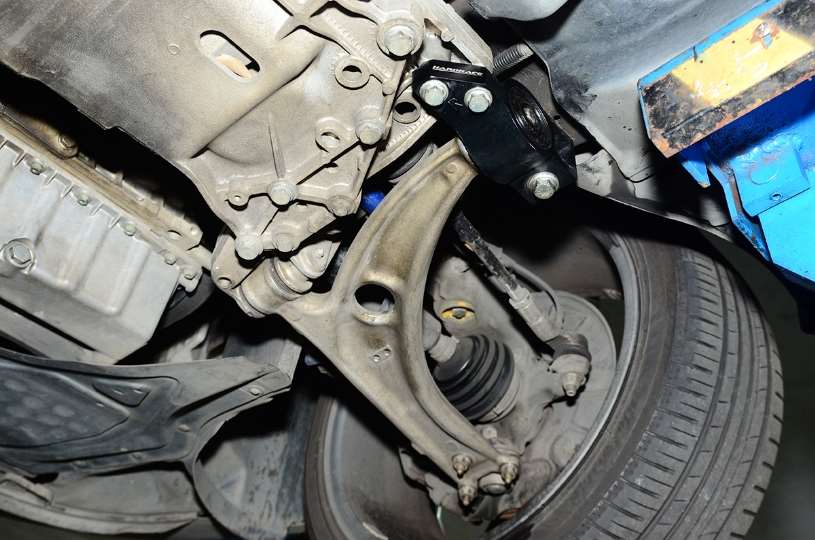
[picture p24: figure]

Smt. Kashibai Navale College of Engineering, Pune | B.E. (Mechanical Engineering)
5

Figure 1.3 – Automobile Lower Control Arm Location

The control arm made with hardened steel and compound with superior quality bushing. A good control arm can regulate the movement of wheels quickly each time you turn or corner.

1.4 – Significance of Project

The suspension system caries the vehicle body and transmit all forces between the body and the road without transmitting to the driver and passengers. The suspension system of a car is used to support its weight during varying road conditions. The suspension system is made of several parts and components. These include the front and rear. The suspension arm gets more attention by many researches like study dynamic analyses of the motor vehicle suspension system using the point-joint coordinate’s formulation. Modeling and simulation are indispensable when dealing with complex engineering systems. It can provide support in all stages of a project from conceptual design, through commissioning and operation. The most effective way to improve product quality and reliability is to integrate them in the design and manufacturing process.

Smt. Kashibai Navale College of Engineering, Pune | B.E. (Mechanical Engineering)
6

### CHAPTER 2: LITERATURE SURVEY

1) M. Sadiq A. Pachapuri, Ravi G. Lingannavar, Nagaraj K. Kelageri, Kritesh K. Phadate, “Design and analysis of lower control arm of suspension system” Materials Today: Proceedings,47(2), May 2021 -

Vehicles ranging from bullock carts to modern vehicles use suspension system such as, leaf springs, pneumatic and hydraulic systems. The main aim of using a suspension system is to prevent the shocks reaching the body of the vehicle from the rough roads and ensure that the vehicle’s wheels remain in contact with the road. There are two types of forces acting on the suspension system of a vehicle, the first is the force from the road disturbance, and the second is the load disturbance. Road unevenness could be of high magnitude and low frequency (such as mountains) and the small magnitude and large frequency (because of rough roads). Load disturbance includes the forces induced by the changing acceleration, braking and cornering. A suspension system should respond very smoothly against road disturbances and should be robust against load disturbances.

In automotive suspension, a control arm is a hinged suspension link between the chassis and the suspension or hub that carries the wheel. The chassis end of a control arm usually rubber busing, is attached by a single pivot. It controls the position of the tire end in only a single degree of freedom, maintaining the radial distance from the chassis mount. The single bushing does not control the arm from moving back and forth; this motion is constrained by a separate link or radius rod. Wishbones are triangular and have two widely spaced chassis bearings, which constrain the tire end of the wishbone from moving back and forth, controlling two degrees of freedom, and without requiring additional links. Most control arms form the lower link of a suspension with few designs using them as the upper link, usually with a lower wishbone. The lower arm should be sturdy, in many cases reported by the users of a particular vehicle, fluttering

Smt. Kashibai Navale College of Engineering, Pune | B.E. (Mechanical Engineering)
7

noise heard over the humps. This paper calculates the forces acting on the lower arm of a four-wheeler with critical loading conditions as the Finite Element Analysis carried for the McPherson type suspension system.

The static analysis performed to determine the location of maximum deflection and stress distribution while the vehicle is stationary and moving over the hump at different speeds. The free-free and constrained modal analysis performed on the suspension arm to find the natural frequency. The fatigue analysis performed to find the life of the arm. Further, by performing topological optimization leads to reduction in the weight. Vehicles ranging from bullock carts to modern vehicles use sus-pension system such as, leaf springs, pneumatic and hydraulic systems. The main aim of using a suspension system is to prevent the shocks reaching the body of the vehicle from the rough roads and ensure that the vehicle’s wheels remain in contact with the road. There are two types of forces acting on the suspension system of a vehicle, the first is the force from the road disturbance, and the second is the load disturbance.

Road unevenness could be of high magnitude and low frequency (such as mountains) and the small magnitude and large frequency (because of rough roads). Load disturbance includes the forces induced by the changing acceleration, braking and cornering. A suspension system should respond very smoothly against road disturbances and should be robust against load disturbances.The suspension system consists of spring, damper and strut. The function of spring is to absorb the shocks and store the energy, but damper (shock absorber) is required to dissipate it. Many types of springs are used in the automobile suspension system like leaf spring, helical coil spring, torsion spring, air spring, etc. Mostly hydraulic or pneumatic dampers are used in the car suspension having a piston and a rod with fluid inside it, which slows down the spring motion. [2]

Smt. Kashibai Navale College of Engineering, Pune | B.E. (Mechanical Engineering)
8
2) Gururaj Dhanu and Prof. R.S.Kattimani, “Comparison Study of Lower Control Arm with Different Materials” International Research Journal of Engineering and Technology, Volume: 03 Issue: 10, Oct 2016 -

In suspension system, the control arm is very important component. The double wishbone suspension system contains lower control arm and upper control arm. The McPherson structural suspension system contains only lower control arm. Between wheel assembly and vehicle chassis the control arms are rigidly placed.
The control arm is connected to the chassis with the help of bush which is placed in pivot joints. Rear and front bushes are used in control arms. it has U-shaped configuration. At the apex of the control arm a ball joint receptacle is formed.

The ball joint receptacle is adapted to cooperate with a ball joint assembly and may include a ball joint housing integrally formed with the control arm. Typical modern control arm incorporates a separate ball joint housing which is inserted in to the apex of control arm. The bushing apertures are designed to retain pipe housings for mating engagement with a pivot bar assembly forming a portion of the vehicle suspension system.

The pivot bar typically extends through both bushing apertures allowing the control arm to pivot about the assembly in response to road conditions affecting the vehicle suspension system. For the construction of control arm high strength alloy steel is used. Control arm consist of modulus section which is between the apex and pivot points. Due to the various functions of control arm, it is one of the important components in suspension system. When vehicle takes turn various types of forces are acting on the wheels which are transmitted to the control arm through attachments such as ball joint assembly and so on, to the wheel. Here in this analysis the main concern is to find out the maximum stress region and stress values in control arm and compare these values with yield strength of materials and the result of experimental testing of control arm at

Smt. Kashibai Navale College of Engineering, Pune | B.E. (Mechanical Engineering)
9

the same load are mentioned in the load case of the control arm.

The lower control arm is an important part of front suspension system. It is used to control wheel trace and transmits the load exerting on the wheel by the ground to the various parts of the car. When the car was in motion, the lower control arm is subjected to complex loads alternating with time. There may be different shapes of lower control arms are available.

The software provides modules to carry out various types of analysis, such as structural analysis, thermal analysis, fluid analysis and computational fluid analysis. The current study involves study of mechanical properties of the material. There are basically two types of analysis one is static analysis and second one is dynamic analysis. Here in this project implicit static analysis is carried out to obtain results. Quadratic tetrahedron is also called ten node tetrahedron. It is second complete polynomial adherent of the isoparametric tetrahedron family. In this element the stress calculation is considerably better than the four nodes. This element proceeds the compensations of the existence of fully automatic tetrahedral mashers.

This is a cad model which can be analyzed to determine structural the stability during turning, to study the behavior of material under different material properties and to compare weight to strength ratio under different material conditions. To study the structural stability of lower control arm under turning conditions. Structural strength of lower control arm is good and safe to manufacture with either steel or aluminum. [3]

3) Mohd Viqaruddina, D.Ramana Reddy, “Structural optimization of control arm for weight reduction and improved performance”, Materials Today: Proceedings, 4(8),January 2017 -

Typical in high performance automotive and aerospace applications is the demand for

Smt. Kashibai Navale College of Engineering, Pune | B.E. (Mechanical Engineering)
10

reduced vehicle mass while maintaining adequate performance and safety. Formula SAE competition is no exception. The nature of the autocross style course favors vehicles with good acceleration capabilities, and both the fuel economy and acceleration events add to the desire for a lightweight vehicle design.

In this paper, discussed the static analysis and torsion analysis of the Control arm by using Radios software and improve the stiffness of the Control Arm and weight reduction of component by changing the geometrical dimension and structural properties. This design is given by topology optimization for compare the base run analysis and optimized analysis. Meshing is carried out by using 10 nodes tetrahedral element in Hyper Mesh & topology optimization is carried out for the given design space.

The topology optimization given the idea of optimum material layout based on load & boundary conditions. Using optimum material layout, the component geometry is finalized by keeping the strength of component constant & 30% reduction in weight. The main objective of this paper is to model and to perform structural analysis of a LOWER CONTROL ARM (LCA) used in the front suspension system, which is a sheet metal component. LCA is modeled in Pro-E software for the given specification. To analyze the LCA, CAE software is used.

The load acting on the control arm are dynamic in nature, buckling load analysis is essential. First finite element analysis is performed to calculate the buckling strength, of a control arm. The FEA is carried out using Solid works stimulation package. The design modification has been done and FEA results are compared.
The influencing parameters which are affecting the response are identified. After getting the final result of finite element analysis optimization has been done using design of experiment method. Taguchi’s design of experiments has been used to optimize the number of experiments. By reducing thickness of the sheet metal and by

Smt. Kashibai Navale College of Engineering, Pune | B.E. (Mechanical Engineering)
11

suggesting the suitable material the production cost of lower control arm is reduced. This leads to cost saving and improved material quality of the product.
Suspension system is an integral part of automobile. It is used to prevent the road shocks being transmitted to vehicle frame and other components of vehicle. Its main function is to provide stability, safety and comfort. It maintains traction between the tyre and road surface. Lower control arm is an important component in the suspension system. It is present in both Mac- Pherson suspension and Double wishbone suspension system. Control arm connect the cars suspension to the actual vehicle frame.

One end of lower control arm is connected to knuckle through a ball joint and other end is attached to vehicle subframe. Lower control arm forms the unsprung weight of vehicle. High unsprung weight complicates wheel control issues under hard acceleration or braking. It may cause severe wheel hop, compromising traction and steering control. Unsprung weight increases the overall weight of suspension system and finally of vehicle.

The main objective of paper is to reduce the unsprung weight of vehicle; by reducing weight of lower control arm using topology optimization. The cost of manufacturing is also reduced. Topology optimization include removing unnecessary material from the base model to reduce weight using given sets of objectives and constraints.

Excess material is removed from the low stressed region of lower control arm. The existing design of left lower control arm from one of the light motor vehicles having Mac-Pherson suspension system is selected for the study (Maruti Suzuki Swift Dzire). It is essential to focus on the stress and deformation study to develop the changes in existing design. FEA approach is used for static structural analysis and topology optimization.

In order to carry out analysis, left lower control arm from one of the LCV is selected

Smt. Kashibai Navale College of Engineering, Pune | B.E. (Mechanical Engineering)
12

having Mac- Pherson suspension system. Reverse engineering of existing lower control arm is done using Coordinate Measuring Machine (CMM). With the help of the coordinates obtained CAD model is generated in CATIA software. In Ansys static structural analysis of control arm is carried out by applying required loading and boundary conditions. Excess material is removed from low stressed region by Topology optimization and the model redesigned and optimized. Static structural analysis of optimized CAD model is done to evaluate stresses and total deformation. [4]

Stability, road handling and comfort of vehicle depend on optimum design of suspension system. Mostly all passenger cars and light trucks use independent suspension system because of inherent advantages over rigid suspension systems. Suspension system is the term given to the system of springs, shock absorbers and linkages that connect a vehicle to its wheels. When a tire hits an obstruction, there is a reaction force and the suspension system tries to reduce this force. The size of this reaction force depends on the unsprung mass at each wheel assembly. In general, the larger the ratio of sprung weight to unsprung weight, the less the body and vehicle occupants are affected by bumps, dips, and other surface imperfections such as small bridges. A large sprung weight to unsprung weight ratio can also impact vehicle control. There are three different types of suspensions namely: Dependent (Rigid Axle), independent and semi -independent suspensions. In the independent suspension system, there are no linkages between two hubs of same axle and it allows each wheel to move vertically without affecting the opposite wheel.

4) Zolkarnain Marjom, Mohd Hafizi Abdul Rahman, Mohd Shukor Salleh, Mohd Suffian Razak, Mohamad Ridzuan Mohamad Kamal, Liza Anuar and Nur Adzly Mohamad Saad, “Introduction of Design and Optimization of Front Lower Control Arm (FLCA) for C-Segment Passenger Car”, International Journal of Engineering & Technology, 71,2018 -

Smt. Kashibai Navale College of Engineering, Pune | B.E. (Mechanical Engineering)
13

In this paper, the design optimization and fabrication process of aluminium cast for front lower control arm (FLCA) were investigated. In this work, the new design concept of front lower control arm is employed. CATIA software was employed in this work to design the concept of the lower control arm. After that, Hyperworks software is used to analyze the structural strength and optimized the weight of the part.

The target of the new design is 20% reduction of the overall weight of the front lower control arm which fabricated using steel material. The obtained results show a significant reduction of the overall weight as high as 25% with a fatigue life cycle 396,000 cycles. This finding proved that the new design of front lower arm has fulfilled the criteria of fatigue life cycle and suitable to be used in a C-segment passenger car.

Stability, road handling and comfort of vehicle depend on optimum design of suspension system. Mostly all passenger cars and light trucks use independent suspension system because of inherent advantages over rigid suspension systems. Suspension system is the term given to the system of springs, shock absorbers and linkages that connect a vehicle to its wheels.

When a tire hits an obstruction, there is a reaction force and the suspension system tries to reduce this force. The size of this reaction force depends on the unsprung mass at each wheel assembly. In general, the larger the ratio of sprung weight to unsprung weight, the less the body and vehicle occupants are affected by bumps, dips, and other surface imperfections such as small bridges. A large sprung weight to unsprung weight ratio can also impact vehicle control. [5]

5) M.H.A. Rahman, M.S. Salleh, A. Abdullah, S.H. Yahaya, M.S.A. Razak, M.R.M. Kamal, Z.Marjom, L.Anuar and N.A.M. Saad, “A new design optimization of light weight front lower control arm” , Journal of Advanced Manufacturing Technology, Volume. 12 No. 1, January - June 2018 -

Smt. Kashibai Navale College of Engineering, Pune | B.E. (Mechanical Engineering)
14

This paper proposed the design optimization of aluminum cast for the front lower control arm was investigated. CATIA software was utilized to design the lower control arm. Hyperworks software was also used to analyze the structural strength and optimize the parts weight. The target of the new design was a 20% weight reduction from the existing part fabricated using steel material. The results showed a significant reduction of the overall weight as high as 25% with a fatigue life cycle approximately 396,000 cycles. Hence, the new design of front lower arm has fulfilled the criteria of fatigue life cycle and is suitable to be used in a C-segment passenger car.

In this literature it presents the design optimization of aluminum cast for the front lower control arm. CATIA software was utilized to design the lower control arm. Hyper works software was also used to analyze the structural strength and optimize the parts weight. The target of the new design was a 20% weight reduction from the existing part fabricated using steel material. The results showed a significant reduction of the overall weight as high as 25% with a fatigue life cycle approximately 396,000 cycles. Hence, the new design of front lower arm has fulfilled the criteria of fatigue life cycle and is suitable to be used in a C-segment passenger car.

Aluminum alloy is widely used in automotive industry in order to give lightweight vehicle and improve energy efficiency. Nowadays aluminum alloy is widely used in body structure and closure such as door, hood, trunk lid and others. For example, Ford F150, 2015 model mostly used Aluminum sheets for the body structures closure panels used “mixed materials” on body structure using aluminum casting, high strength steels and sheet metals

There are many components involved in the front suspension assembly such as knuckle, lower control arm, spring, etc. This study focused on front lower control arm (FLCA) as a target light weight component. FLCA is a connecting linkage between knuckles to

Smt. Kashibai Navale College of Engineering, Pune | B.E. (Mechanical Engineering)
15

sub frame underneath vehicle. In general, lower control arm design needs to be robust to enable multi-loading and lighter weight as it serves as the main hardpoint alignment. As a part of chassis structure components, it plays a major role in anchoring suspension of hard points for lateral and longitudinal loading. In platform development of a vehicle, depending on vehicle crash strategies, lower control arm as well is to absorb or delay crash energy, particularly in crucial crash case such as 45° offset frontal impact.

The commercial part of front lower control arm is fabricated from metal stamping process. The main objective of this research is to design a new lightweight of front lower control arm for the C-Segment vehicle using topology optimization process. After several iterations of design and optimization process of aluminum cast FLCA, the weight reduction of aluminum cast FLCA achieved the target of 20%.

Based on the final design concept of FLCA, the total weight is 2.55 kg, which is about 25% of weight reduction compared with the current metal stamping FLCA weight 3.40 kg and still maintains the structural strength performance and fatigue durability performance. The new design of this aluminum cast lower control arm has unique design compared with the current commercial design.
It has shown some novelty in term of the design shape of the body part with a combination of the aluminum cast for body parts and also sleeve metal stamping for at rear lower control arm bush hardpoint. The I-beam cross section provides higher stiffness and moment for the parts to sustain the higher bending moment. [6]
6) Kale AR, Tadamalle AP and Patil ND, “Analysis and Optimization of Lower Control Arm”, Crimnson publishers, Evolution in mechanical engineering, ISSN: 2640-9690, August 07, 2018 -

Control arm in automotive vehicle acts as a linkage between sprung and unsprung mass of vehicle. Lower control arm is subjected to various loads. Due to this type of loading, there are chances of bending of control arm. Hence failure of lower control arm occurs.

Smt. Kashibai Navale College of Engineering, Pune | B.E. (Mechanical Engineering)
16

Weight reduction of vehicle component is one of the main concerns. The aim of the paper is to analyze and optimize the lower arm using finite element analysis. The model of lower control arm is done in CAD software.

In this research it presents to analyze and optimize the lower arm using finite element analysis. Control arm in automotive vehicle acts as a linkage between sprung and unsprung mass of vehicle.Weight reduction of vehicle component is one of the main concerns. The model of lower control arm is done in CAD software. Topology optimization of lower arm is performed for weight reduction. After topology optimization static analysis of optimized lower control arm is carried out.

Results obtained from analysis were studied to check whether the design is within the yield strength. Cost analysis of existing and optimized lower control arm has been carried out to know the cost effectiveness. The purpose of automobile suspension system is passenger comfort and vehicle control. The result of stress generated by static analysis of existing lower control arm is 223.62MPa. After optimization the result obtained for stress analysis of optimized lower control arm is 240.59MPa. Thus, the design is safe according to yield strength criteria. The weight of existing lower control arm is 2.6042kg and that of optimized part is 2.203kg. Thus, the weight reduction is 15.39% by using optimized control arm. The cost saving by using optimized lower control arm over existing control arm is 8.8%. [7]

7) Swapnil S. Khode, Prof. Amol N. Patil, Prof. Amol B. Gaikwad, “Design Optimization of a Lower Control Arm of Suspension System in an LCV by using Topological Approach”, International Journal of Innovative Research in Science, Engineering and Technology Volume 6, Issue 6, June 2017 -

The most important component in vehicle is a suspension system, which directly affects the safety, performance and noise level. The unsprung mass is the mass of the suspension components which is directly connected to them, rather than supported by the suspension. High unsprung weight exacerbates issues like wheel control, ride quality

Smt. Kashibai Navale College of Engineering, Pune | B.E. (Mechanical Engineering)
17

and noise. Unsprung weight includes the mass of components such as the wheel axles, wheel bearings, wheel hubs, springs, shock absorbers, and Lower Control Arm. The lower control arm is a wishbone-shaped metal strut that attaches the wheel to the vehicle's frame.

Different optimization techniques under various load conditions have been widely used in automobile sector for lightweight and functioning enhancement. This study deals with Finite Element Analysis of the Lower control arm of Mac-pherson suspension system and its optimization under static loading condition. This journal deals with Finite Element Analysis of the Lower control arm of Mac-pherson suspension system and its optimization under static loading condition. The existing design of lower control arm from one of the light commercial vehicles. In order to determine the deformation and stress distribution in the current design, the finite element analysis is carried out.

In this research it presents to optimize the lower control arm of Mac-pherson suspension system under the current boundary conditions for weight reduction. The baseline model of the lower control arm is created by using solid modelling software viz. CATIA. ANSYS Workbench is used for Finite Element Analysis and OPTISTRUCT solver module is used to generate the optimized model. The weight reduction in one lower control arm is observed to be 17.5%. As deflection and stress of modified LCA is within the range. In topology optimization process using Hyperworks Optistruct software, the base concept design was optimized based on standard suspension abusive load cases loading at FLCA hardpoint as shown in Table 1. The topology optimization is a method to optimize the design in design space with the constraint of loads and some boundary conditions. It is a stress-based optimization through load path on the geometry.
It gives the best selection of design based on load path on material to reduce the weight of material. In terms of FLCA design, the non-load path areas based on suspension abusive loading were eliminated to reduce the material. This process was done in several iterations to get the optimum minimum of 20% weight reduction as shown in Figure.

Smt. Kashibai Navale College of Engineering, Pune | B.E. (Mechanical Engineering)
18

The lower control arm is the most vital component in a suspension system. There are two control arms, lower control arm and upper control arm. Lower control arm allows the up and down motion of the wheel. It is usually a steel bracket that pivots on rubber bushings mounted to the chassis. The other end supports the lower ball joint. Significant number of loads are transmitted through the control arm while it serves to maintain the contact between the wheel and the road and thus providing the precise control of the vehicle. There are many types of control arms are available. The selection of the arm is mainly based on the type of suspension system. Thus, the modified design is safe. Weight of the final optimized model is 0.99 kg. The total reduction in mass is observed 17.5% by keeping Factor of safety for optimized design within permissible limits. Thus, the objective of weight reduction of unsprung mass and cost reduction has been achieved. [8]

8) Yong-Dae Kim, Jae-Eun Jeong, Jin-Su Park, In-Hyung Yang, Tae-Sang Park, Pauziah Binti Muhamad, Dong-Hoon Choi, Jae-Eung Oh, “Optimization of the lower arm of a vehicle suspension system for road noise reduction by sensitivity analysis”, Mechanism and Machine Theory, 69, 278–302, 2013 -

As advances in automotive design and manufacturing technology have emerged, the demand for noise reduction and ride quality improvement has increased. In particular, under normal driving conditions, drivers are most exposed to road noise, which can be unpleasant. Furthermore, it can reduce ride quality and brand awareness. Noises within the passenger compartment are categorized as structural and air-borne noises, depending on the transfer path characteristics.

This journal introduces an analyzed characteristics of road noise using vehicle tests and identified the 200– 230 Hz range as the most important frequency for road noise reduction. Moreover, vibration sources in the vehicle suspension system were identified through transfer path analysis and coherence analysis. In order to achieve noise

Smt. Kashibai Navale College of Engineering, Pune | B.E. (Mechanical Engineering)
19

reduction using sensitivity analysis, the lower arm of the vehicle suspension system was found to be the most important design variable.

For design optimization, we employed a robust and efficient sequential approximate optimization method, named PQRSM (Progressive Quadratic Response Surface Method) suitable for solving practical design optimization problems. The estimates based on a model proposed from optimization were in accord with the results of the experiment and road noise reduction was achieved by applying the optimally designed lower arm of the vehicle suspension system to a real vehicle. This study identified the vibration sources of the vehicle suspension system with superior coherence and proposed an optimal design to reduce road noise that is structure-borne noise and obtained to the following conclusions. [9]

9) Liang Tang, JieWu, Jinhao Liu, Cuicui Jiang, and Wen-Bin Shangguan, “Topology Optimization and Performance Calculation for Control Arms of a Suspension” by Hindawi Publishing Corporation Advances in Mechanical Engineering, Article ID 734568, Volume 2014 -

Lower control arm is an important part in the suspension system. It is connected between subframe and knuckle. It holds the vehicle wheels in alignment. High unsprung weight complicates steering control and traction control issues. This paper deals with the reduction of unsprung mass of vehicle by topology optimization of lower control arm. For analysis existing lower control arm of Mac- Pherson suspension system is selected. In this journal it presents the topology optimization model including ball joints and bushing for topology optimization of an aluminum CA is established, where a ball joint is simplified as rigid elements and the elastic properties of a rubber bushing are estimated using Mooney-Rivlin constitutive law.

Smt. Kashibai Navale College of Engineering, Pune | B.E. (Mechanical Engineering)
20

A method for treating with multiple loads in topology optimization of CA is presented. Inertia relief theory is employed in the FEA model of the CA in order to simulate the large displacement motion characteristics of the CA. ACA is designed based on the topology optimization results, and the strength, natural frequency, and rigidity of the optimized CA are calculated.

The main contribution of this paper is the establishment of the topology optimization model for the CA with considerations of the elastics of ball joints and rubber bushings, and the method for treating with multiple loads in topology optimization of CA. The topology optimization results are compared with and without the modeling the stiffness of ball joints and rubber bushings. It is concluded that the elastics of ball joints and bushings should be modeled in the topology optimization of a Control Arm in order to meet the requirements of stress, stiffness, and first order natural frequency for the Control Arm.

The Topology optimization gives the optimum material layout according to the design space and loading condition using given sets of objectives and constraints. The main aim of topology optimization is to reduce weight by removing excess material from low stressed region. To solve any topology optimization problem, three parameters must be specified, namely design variables (material density), design objective (weight reduction) and design constraints (volume) Topology optimization is used to generate optimal shape of mechanical structure. Deformation in optimized model is found to be

### 8.84 mm. The maximum deformation of optimized design and existing design are not

varying by considerable amount. The actual lower control arm is designed by analyzing CAD model. Pockets are made on the surface of control arm according to the CAD model. Structural analysis is done to determine the stress distribution and deformation by applying mechanical load. Critical areas of location predicted where the stress distribution is high. The yield strength of material is 415 MPa and generated von-Mises stress in lower control arm should be less than yield strength of material. [10]

Smt. Kashibai Navale College of Engineering, Pune | B.E. (Mechanical Engineering)
21

### CHAPTER 3: PROBLEM DEFINITION AND OBJECTIVES

### 3.1 Problem Definition:

Chassis parts are a critical part of a vehicle, leaving no room for error in the design and quality the present process relates to a computer-aided structure analysis and design graphic display device and method, and more particularly, to a computer-aided structure analysis of A control arm and which is analyzed and designed, thereby meet the customer requirements of LCA.

This project is to optimize the A control arm by doe FFT analyzer and Impact Hammer Test by suggesting suitable material, and reducing sheet metal thickness, to reduce the batch production cost and to increase the strength of LCA.

### 3.2 Objectives:

1. To prepare CAD design using CATIA V5.

### 2. Static structural Analysis of Automotive A type control arm

3. Optimization of Automotive A type control arm.
4. To perform static structural analysis of the suspension arm using ANSYS Software.

### 5. To optimize the lower control arm for weight reduction” (unsprung weight) up to

5-20% and suggest alternate design.

### 6. Testing and validation of Automotive A type control arm with the help of

Universal Testing Machine.

### 7. To compare the factor of safety for optimized and baseline design of lower

control arm by keeping factor of safety for optimized design within permissible limits.
8. To perform experimentation on physical model of Lower Control Arm.

Smt. Kashibai Navale College of Engineering, Pune | B.E. (Mechanical Engineering)
22

### CHAPTER 4: METHEDOLOGY

The methodology of our project would be starting with the topic selection, then working on the topic by researching and creating a detailed plan for execution of the project. Then executing the project by manufacturing and then testing the model of the project. Then at last finishing the miscellaneous work and concluding the Project. The following is the stepwise proposed technical methodology:

- CAD Modeling of Existing Lower Control Arm –
To prepare CAD design using CATIA V5 and Solidworks. The CAD model is prepared to apply all the dimensions and the features of the component in the analysis of the component.
- Analysis of Design in FEA of existing lower control arm
Static structural Analysis of Automotive A type control arm. To find out the stiffness, buckling strength of the existing model.
- Apply Topology Optimization on the design and analyze
Topology optimization (TO) is a shape optimization method that uses algorithmic models to optimize material layout within a user-defined space for a given set of loads, conditions, and constraints. Optimization of Automotive A type control arm.
- Modified Design as per topological optimization and analyze again
To find out the stiffness, buckling strength of the new model. To optimize the lower control arm for weight reduction (unsprung weight) up to 5-20% and suggest alternate design.
- Obtain the optimized results
The results are obtained according to the applied parameters to the model in the software.


Smt. Kashibai Navale College of Engineering, Pune | B.E. (Mechanical Engineering)
23
- Model analysis of selected design
Finite element values of the existing design and new designs are compared and better design is identified. Influencing parameters which are affecting the response are identified. The results obtained are compared with the real time so that the results match. Finally, the analysis becomes successful.
- Testing and validation of lower control arm.
Testing and validation of Automotive A type control arm with the help of Universal Testing Machine.

Table 1 - Flowchart for the Methodology

Smt. Kashibai Navale College of Engineering, Pune | B.E. (Mechanical Engineering)
24

### CHAPTER 5: DESIGN, ANALYSIS AND DESIGN OPTIMIZATION

### 5.1 FEA (FINITE ELEMENT ANALYSIS)

The finite element method (FEM), is a numerical method for solving problems of engineering and mathematical physics. Typical problem areas of interest
include structural analysis, heat transfer, fluid flow, mass transport, and electromagnetic potential. The analytical solution of these problems generally require the solution
to boundary value problems for partial differential equations. The finite element method formulation of the problem results in a system of algebraic equations. The method yields approximate values of the unknowns at discrete number of points over the domain. To solve the problem, it subdivides a large problem into smaller, simpler parts that are called finite elements.

Finite element analysis is based on principles that include boundary conditions, such as forces and pressures, as well as three governing equations:

- Equilibrium equations, which find when the opposing forces or influences are balanced.
- Strain-displacement relations, which measure the deformation that the design experiences under any given external impacts.
- Constitutive equations, which are relations between two physical quantities, specific to the given metal or substance, which predict the material's response to external stimuli.

For finite element analysis to perform its necessary simulations, a mesh -- containing millions of small elements that together form the shape of a structure -- must be created. Calculations must be performed on every single element; the combination of each of these individual answers provides the final result for the full structure.


Smt. Kashibai Navale College of Engineering, Pune | B.E. (Mechanical Engineering)
25

CAD: -

Fig. 5.1 - CATIA model

Fig.5.2 - Drafting of existing model


Smt. Kashibai Navale College of Engineering, Pune | B.E. (Mechanical Engineering)
26

Fig.5.3 – Complete Model Assembly

Fig.5.4 – Ball Joint CAD

Fig.5.5 – Ball Joint CAD

Smt. Kashibai Navale College of Engineering, Pune | B.E. (Mechanical Engineering)
27

In present research for analysis ANSYS (Analysis System) software is used. Basically, its present FEM method to solve any problem. Following are steps in detail

### 1. Geometry 2. Discretization (Meshing) 3. Boundary condition 4. Solve (Solution) 5. Interpretation of results

Step 1: Details of material namely copper, steel, grey cast iron, composite material, fluid domain material is defined in engineering data. i.e., ANSYS default material is structural steel.
Step 2: Import of geometry created in any CAD software namely CATIA, PRO E, SOLIDWORK, INVENTOR etc. in geometry section. If any correction is to be made it can be created in geometry section in Design modeller or space claim.
Step 3: In model section after import of component
- Material is assigned to component as per existing material
- Connection is checked in contact region i.e., bonded, frictionless, frictional, no separation etc. for multi body components.
- Meshing or discretization is performed i.e., to break components in small pieces (elements) as per size i.e., preferably tetra mesh and hexahedral mesh for 3D geometry and for 2 D quad or trial are generally preferred.
Step 4: Boundary condition are applied as per analysis namely in fixed support, pressure, force, displacement, velocity as per condition.
Step 5: Now problem is well defined and solve option is selected to obtain the solution in the form of equivalent stress, strain, energy, reaction force etc.


Smt. Kashibai Navale College of Engineering, Pune | B.E. (Mechanical Engineering)
28

Table 2 - Table of Material properties

Material | Structural Carbon Steel – ASTM A36
Tensile Ultimate Strength | 460 MPA
Tensile Yield Strength | 250 MPA
Young’s Modulus | 2x10^11 PA
Poission’s Ratio | 0.3
Bulk Modulus | 1.6667x10^11 PA
Shear Modulus | 7.6923x10^11 PA

Fig.5.6 - Existing design of lower control arm


Smt. Kashibai Navale College of Engineering, Pune | B.E. (Mechanical Engineering)
29

Fig.5.7 - Meshing of model

Table 3 - Meshing of model

Elements Details:

Table 4 - Elements Details

### 5.2 Boundary Condition

A boundary condition for the model is the setting of a known value for a displacement or an associated load. For a particular node you can set either the load or the displacement but not both.


Smt. Kashibai Navale College of Engineering, Pune | B.E. (Mechanical Engineering)
30

The main types of loading available in FEA include force, pressure and temperature. These can be applied to points, surfaces, edges, nodes and elements or remotely offset from a feature. The way that the model is constrained can significantly affect the results and requires special consideration. Over or under constrained models can give stress that is so inaccurate that it is worthless to the engineer. In an ideal world we could have massive assemblies of components all connected to each other with contact elements but this is beyond the budget and resource of most people. We can however, use the computing hardware we have available to its full potential and this means understanding how to apply realistic boundary conditions.

Details of Model:

Vehicle Name - Maruti Suzuki Baleno
Weight – 865 KG
So 865 x 9.81 = 8485 N
Weight on Each Wheels Considered as – 8485/4 = 2121.4 N

Fig.5.8 - Boundary condition of model Total Deformation

The total deformation & directional deformation are general terms in finite element methods irrespective of software being used. Directional deformation can be put as the


Smt. Kashibai Navale College of Engineering, Pune | B.E. (Mechanical Engineering)
31

displacement of the system in a particular axis or user defined direction. Total deformation is the vectors sum all directional displacements of the systems.

Fig.5.9 - Total Deformation of model Steps in Topology Optimization
The topology optimization consists of the following sequence of steps.
- Define the design space
- Define optimization parameters
- Material removal process and detail design
Step 1: Details of material namely copper, steel, grey cast iron, composite material, fluid domain material is defined in engineering data. i.e., ANSYS default material is structural steel.
Step 2: Import of geometry created in any CAD software namely CATIA, PRO E, SOLIDWORK, INVENTOR etc. in geometry section. If any correction is to be made it can be created in geometry section in Design modeller or space claim.
Step 3: In model section after import of component
- Material is assigned to component as per existing material
- Connection is checked in contact region i.e., bonded, frictionless, frictional, no separation etc. for multi body components.


Smt. Kashibai Navale College of Engineering, Pune | B.E. (Mechanical Engineering)
32
- Meshing or discretization is performed i.e., to break components in small pieces (elements) as per size i.e., preferably tetra mesh and hexahedral mesh for 3D geometry and for 2 D quad or trial are generally preferred.
Step 4: Boundary condition are applied as per analysis namely in fixed support, pressure, force, displacement, velocity as per condition.
Step 5: Now problem is well defined and solve option is selected to obtain the solution in the form of equivalent stress, strain, energy, reaction force etc.
Step 6: Topology optimization tool is selected from ANSYS list view and drag and dropped in solution section of static structural so that it takes its all-boundary condition, geometry, all details and perform topology optimization on selected component.
Step 7: Define the topology density and element density section as output. After performing topology algorithm on component, selected parts contain red, brown and grey colour on it. So, red region colour indicates material removal area along with marginal (brown colour) and grey colour to keep material.
Step 8: After selection of specific shape material is removed from component and reanalysis of component is performed to observe the sustainability of existing optimized component under same boundary condition.

Fig.5.10 - Boundary condition for topology optimization region


Smt. Kashibai Navale College of Engineering, Pune | B.E. (Mechanical Engineering)
33

Fig.5.11 - Topology optimized results

Fig.5.12 - Topology optimized results

- Red region indicates material removal area region.


Smt. Kashibai Navale College of Engineering, Pune | B.E. (Mechanical Engineering)
34

Fig.5.13 - Optimized lower control arm

Fig.5.14 - Details of optimized lower control arm

Table 5 - Details of optimized lower control arm


Smt. Kashibai Navale College of Engineering, Pune | B.E. (Mechanical Engineering)
35

Fig.5.15 - Boundary condition for optimized lower control arm

Fig.5.16 - Optimized lower control arm deformation result


Smt. Kashibai Navale College of Engineering, Pune | B.E. (Mechanical Engineering)
36

Fig.5.17 - Optimized lower control arm equivalent stress result

Fig.5.18 - Optimized lower control arm equivalent strain result

- Strain is observed around 371 microns.

Smt. Kashibai Navale College of Engineering, Pune | B.E. (Mechanical Engineering)
37

### 5.3 Experimental Test

A Universal Testing Machine (UTM) is used to test both the tensile and compressive strength of materials. Universal Testing Machines are named as such because they can perform many different varieties of tests on an equally diverse range of materials, components, and structures.

Universal Testing Machines can accommodate many kinds of materials, ranging from hard samples, such as metals and concrete, to flexible samples, such as rubber and textiles. This diversity makes the Universal Testing Machine equally applicable to virtually any manufacturing industry.

Table 6 – Specification of Universal Testing Machine

1 | Max Capacity | 400KN
2 | Measuring range | 0-400KN
3 | Least Count | 0.04KN
4 | Clearance for Tensile Test | 50-700 mm
5 Clearance for Compression | Test | 0- 700 mm
6 | Clearance Between column | 500 mm
7 | Ram stroke | 200 mm


Smt. Kashibai Navale College of Engineering, Pune | B.E. (Mechanical Engineering)
38
8 | Power supply | 3 Phase, 440Volts, 50 cycle. A.C
9 Overall dimension of | machine (L*W*H) | 2100*800*2060
10 | Weight | 2300Kg

Fig.5.16 - Testing in Universal Testing Machine


Smt. Kashibai Navale College of Engineering, Pune | B.E. (Mechanical Engineering)
39

Fig.5.17 - Experimental testing results

Table 7 -Evaluation of Results
S. No | Parameters | Existing component | Optimized component
d1 | Deformation (mm) | Max | 2.593mm | 2.869 mm
| | Min | 0 mm | 0 mm
2 Von-mises stress | (Mpa) | Max | 350.22 Mpa | 399 Mpa
| | Min | 0.0012 MPa | 0.0014 MPa
3 | Mass reduction | | 2.55 | 2.39 | 6.07% weight reduction
4 | Factor of Safety | 1.31 | | 1.15

Smt. Kashibai Navale College of Engineering, Pune | B.E. (Mechanical Engineering)
40

### CHAPTER 6: RESULTS AND DISCUSSION

### 6.1 Results obtained from the project

Elements Details of Ansys -
- Nodes – 28547 for Existing component and 27382 for Optimized component.
- Elements - 14197 for Existing component and 13451 for Optimized component. Universal Testing Machine Results -
- The Deformation Maximum is 2.593mm for Existing component and 2.869 mm for Optimized component.
- The Deformation Minimum is 0mm for Existing component and 0mm for Optimized component.
- The Von-mises stress Maximum are 350.22 MPA for Existing component and 399 MPA for Optimized component.
- The Von-mises stress Minimum are 0.0012 MPa for Existing component and 0.0014 MPA for Optimized component.
- Mass of the Existing component is 2.55 KG for Existing component and 2.39 KG (6.07% weight reduction) for Optimized component.
- Factor of Safety of the Existing component is 1.31 for existing component and 1.15 for Optimized component.

The existing design has been modified, by reducing the thickness of the existing profile. The optimization of lower control arm is done by applying the Design of Experiments method. The parameters are identified. The FEA is done on LCA and the buckling load has been compared with the existing component. The sheet metal thickness of the new design has been reduced from 3.6 mm to 3mm. For the mass production the cost has been reduced to Rs.34000 for 2000 products in a batch as assumed. For the modified design the structural rigidity has been increased for the LCA, when compared to the existing design. Finally, mass of the control arm has been reduced up to 6.07 % when compared with existing model.

Smt. Kashibai Navale College of Engineering, Pune | B.E. (Mechanical Engineering)
41

### CHAPTER 7: CONCLUSION

This project can be extended to satisfy the following requirements as the key objectives:

- Implementing new design changes in the existing model can be done
- Identifying more materials for the proposed design and new design
- Increasing the number of levels of the response
- Based on observations design improvements will be made in terms of shape, size and material based on design modification objectives.
- The study will focus on existing design performance, advantage and limitations.

As deflection and stress of modified Lower Control Arm is within the range. Thus, the modified design is safe. Weight of the final optimized model is 2.39 kg. The total reduction in mass is observed 6.07% by keeping Factor of safety for optimized design within permissible limits.

Thus, the objective of weight reduction of unsprung mass and cost reduction has been achieved.

Smt. Kashibai Navale College of Engineering, Pune | B.E. (Mechanical Engineering)
42

### REFERENCES AND BIBLIOGRAPHY

[1] Mohd Hafizi Abdul Rahman, Mohd Shukor Salleh, Mohd Suffian Razak, Mohamad Ridzuan Mohamad Kamal, Zolkarnain Marjom, Liza Anuar and Nur Adzly Mohamad Saad, “Introduction of Design and Optimization of Front Lower Control Arm (FLCA) for C-Segment Passenger Car”, International Journal of Engineering & Technology, 71,2018.
[2] M. Sadiq A. Pachapuri, Ravi G. Lingannavar, Nagaraj K. Kelageri, Kritesh K. Phadate, “Design and analysis of lower control arm of suspension system” Materials Today: Proceedings,47(2), May 2021.
[3] Gururaj Dhanu and Prof. R.S.Kattimani, “Comparison Study of Lower Control Arm with Different Materials” International Research Journal of Engineering and Technology, Volume: 03 Issue: 10, Oct 2016.
[4] Mohd Viqaruddina, D.Ramana Reddy, “Structural optimization of control arm for weight reduction and improved performance”, Materials Today: Proceedings, 4(8),January 2017
[5] Zolkarnain Marjom, Mohd Hafizi Abdul Rahman, Mohd Shukor Salleh, Mohd Suffian Razak, Mohamad Ridzuan Mohamad Kamal, Liza Anuar and Nur Adzly Mohamad Saad, “Introduction of Design and Optimization of Front Lower Control Arm (FLCA) for C-Segment Passenger Car”, International Journal of Engineering & Technology, 71,2018.
[6] M.H.A. Rahman, M.S. Salleh, A. Abdullah, S.H. Yahaya, M.S.A. Razak, M.R.M. Kamal, Z.Marjom, L.Anuar and N.A.M. Saad, “A new design optimization of light weight front lower control arm” , Journal of Advanced Manufacturing Technology, Volume. 12 No. 1, January - June 2018.
[7] Kale AR, Tadamalle AP and Patil ND, “Analysis and Optimization of Lower Control Arm”, Crimnson publishers, Evolution in mechanical engineering, ISSN: 2640-9690, August 07, 2018.

Smt. Kashibai Navale College of Engineering, Pune | B.E. (Mechanical Engineering)
43
[8] Swapnil S. Khode, Prof. Amol N. Patil, Prof. Amol B. Gaikwad, “Design Optimization of a Lower Control Arm of Suspension System in an LCV by using Topological Approach”, International Journal of Innovative Research in Science, Engineering and Technology Volume 6, Issue 6, June 2017.
[9] Yong-Dae Kim, Jae-Eun Jeong, Jin-Su Park, In-Hyung Yang, Tae-Sang Park, Pauziah Binti Muhamad, Dong-Hoon Choi, Jae-Eung Oh, “Optimization of the lower arm of a vehicle suspension system for road noise reduction by sensitivity analysis”, Mechanism and Machine Theory, 69, 278–302, 2013.
[10] Liang Tang, JieWu, Jinhao Liu, Cuicui Jiang, and Wen-Bin Shangguan, “Topology Optimization and Performance Calculation for Control Arms of a Suspension” by Hindawi Publishing Corporation Advances in Mechanical Engineering, Article ID 734568, Volume 2014.
[11] Hazem ali attia, “Dynamic modeling of the double wishbone motor-vehicle suspension system”, European journal of mechanics A/solids 21, 167-174, 2002.
[12] J.C. fauroux, B.C. bouzgarrou, “Dynamic obstaclecrossing of a wheeled rover with double wishbone suspension”. French institute for advanced mechanics (IFMA), EA3867, FR TIMS / CNRS 2856.
[13] Vdovin D & Chichekin I (2016), Loads and Stress Analysis Cycle Automation in the Automotive Suspension Development Process. Procedia Engineering 150, 1276–1279.
[14] Nikoo MF, Azizi H, Parvin N & Naghibi HY (2016), The influence of heat treatment on microstructure and wear properties of friction stirs welded AA6061-T6 / Al 2 O 3 nanocomposite joint at four different traveling speed. Journal of Manufacturing Processes 22, 90–98.
[15] Design optimization of a carbon fiber reinforced composite automotive lower arm, Do-Hyoung Kim a, Dong-Hoon Choi a, HakSung Kim, Composites: Part B 58 (2014) 400–407.
[16] Kim Y, Jeong J, Park J, Yang I, Park T, Muhamad PB, Choi D & Oh J (2013), Optimization of the lower arm of a vehicle suspension system for road noise

Smt. Kashibai Navale College of Engineering, Pune | B.E. (Mechanical Engineering)
44

reduction by sensitivity analysis. DOI: 10.1016/j.mechmachtheory.2013.06.010.
[17] Chen JK, Hung HY, Wang CF & Tang NK (2017), Effects of casting and heat treatment processes on the thermal conductivity of an Al-Si-Cu-Fe-Zn alloy. International Journal of Heat and Mass Transfer 105, 189–195.
[18] Dae Sung Joo, Nizar AL-Holou, Jonathan M. Weaver, Tarek Lahdhirt, and Faysal Al-Abbas, “Nonlinear modeling of vehicle suspension system”, American control conference, vol. 1, 2000, pp 115-119.
[19] Dong-Chan Lee and Jeong-Ick Lee, “Structural optimization concept for the design of an Aluminium control arm”, Proceedings of The Institution of Mechanical Engineers Part D-journal of Automobile Engineering, vol. 217, 2003, pp 647-656.
[20] Hiten kumar Patel, “optimization of an aerospace component die design using metal forming simulation capability of hyper-form” HTC (hyper- works technology conference) 2008, pp 6-7.


Smt. Kashibai Navale College of Engineering, Pune | B.E. (Mechanical Engineering)
45

### PHOTOGRAPH OF LOWER CONTROL ARM MODEL

Smt. Kashibai Navale College of Engineering, Pune | B.E. (Mechanical Engineering)
46

### WORK FLOW

Work | Start Date | Finishing Date
General Planning | 15/08/2022 | 29/08/2022
Approval | 03/09/2022 | 27/09/2022
Purchasing | 28/09/2022 | 02/10/2022
Design | 03/11/2022 | 17/11/2022
Analysis of Exiting Component | 18/11/2022 | 02/12/2022
Testing of Existing Component | 03/12/2022 | 13/12/2022
Analysis for optimization | 15/12/2022 | 21/01/2023
Design of Optimized Component | 22/01/2022 | 01/02/2023
Fabrication of Optimized Component | 02/02/2023 | 16/02/2023
Testing of Optimized Component | 17/02/2023 | 20/02/2023
Project Finishing | 21/02/2023 | 26/02/2023

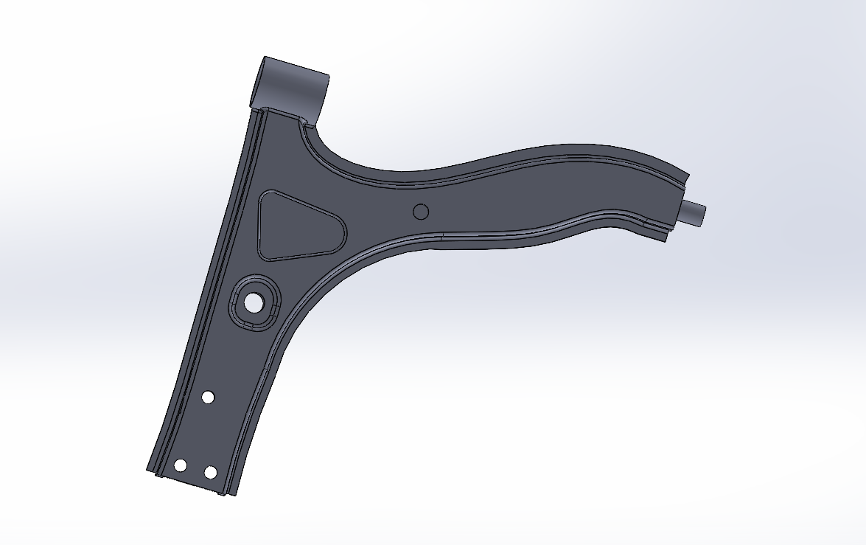
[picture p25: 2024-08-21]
PICTURES/Screenshot (765).png

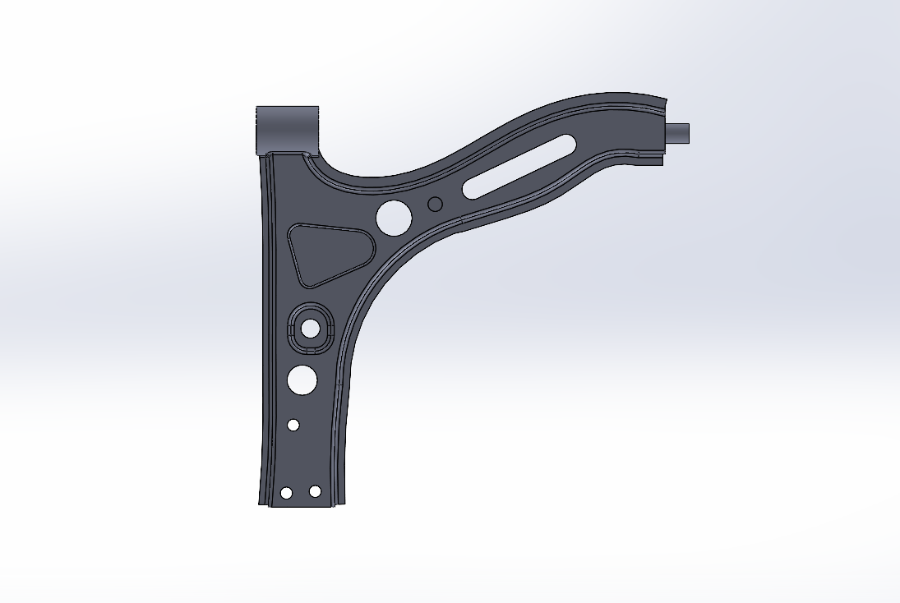
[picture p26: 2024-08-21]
PICTURES/Screenshot (767).png

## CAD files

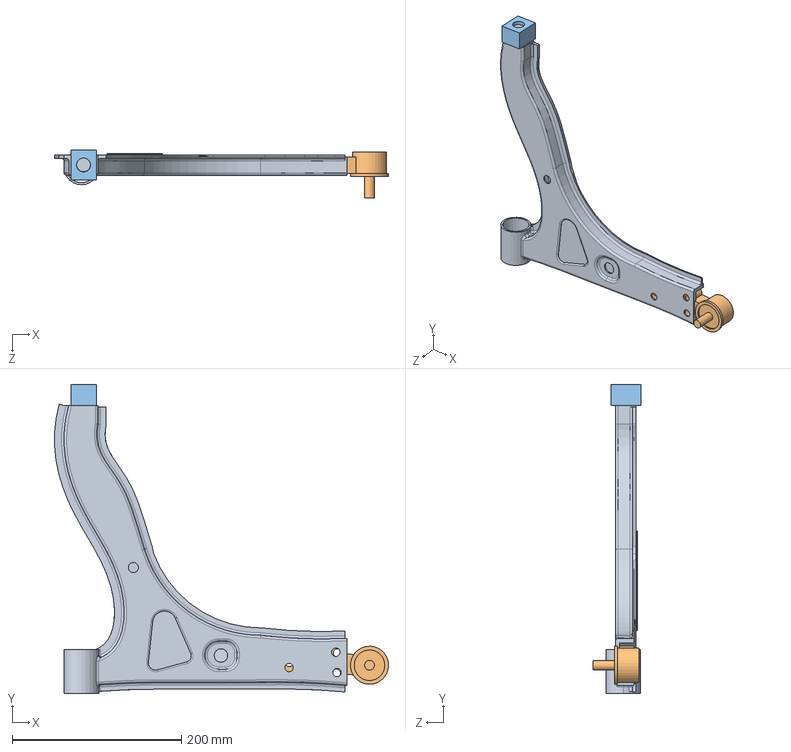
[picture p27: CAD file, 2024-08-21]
CAD/Assem1.SLDASM
394.5 x 365.4 x 56.3 mm
L.Co1
Ball Joint
Bush

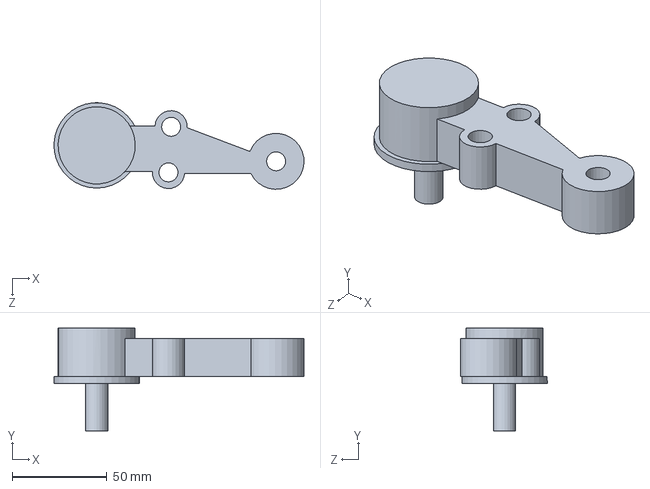
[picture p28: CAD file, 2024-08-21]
CAD/Ball Joint.SLDPRT
131.6 x 54.0 x 45.6 mm

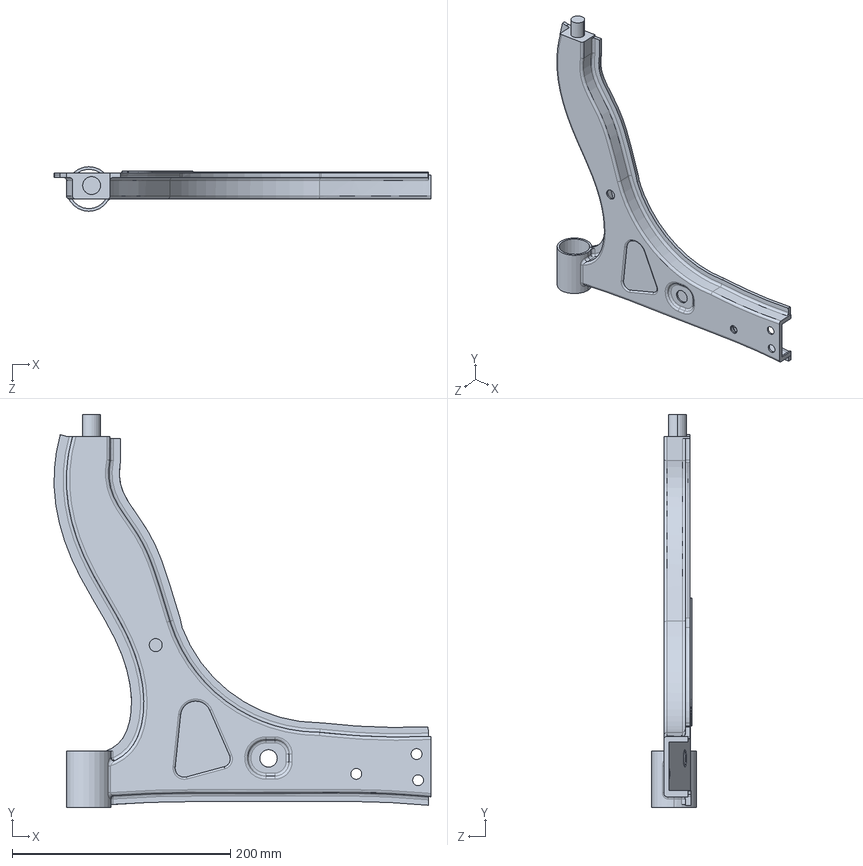
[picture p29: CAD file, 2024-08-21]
CAD/L.C.Aff.SLDPRT
345.4 x 360.4 x 41.0 mm

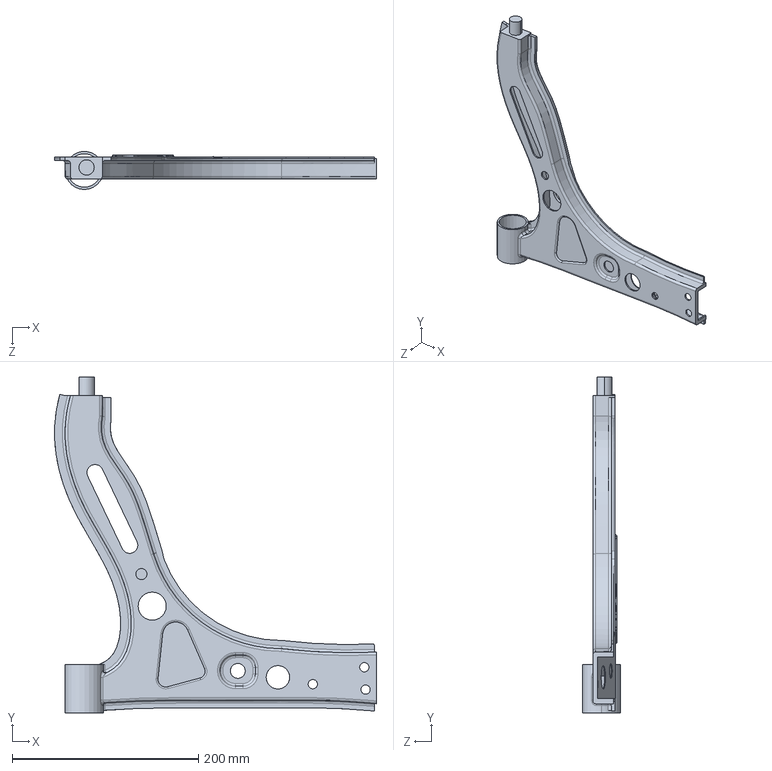
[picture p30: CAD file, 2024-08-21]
CAD/FF.SLDPRT
345.5 x 360.4 x 40.8 mm

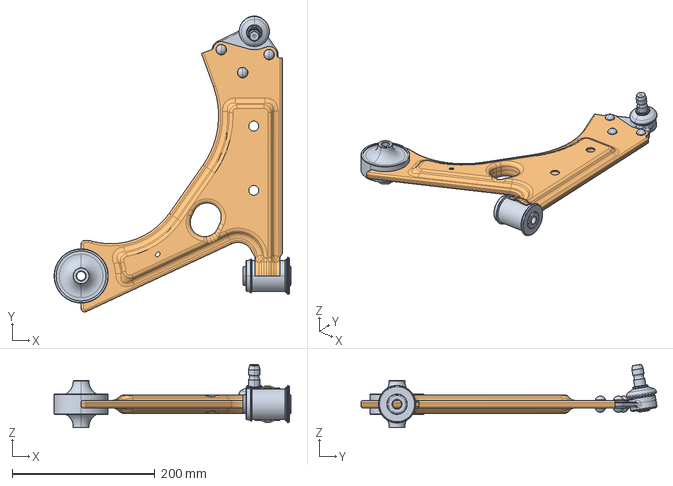
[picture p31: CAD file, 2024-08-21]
CAD/Corsa D Lower Control Arm.stp
331.9 x 414.9 x 88.8 mm

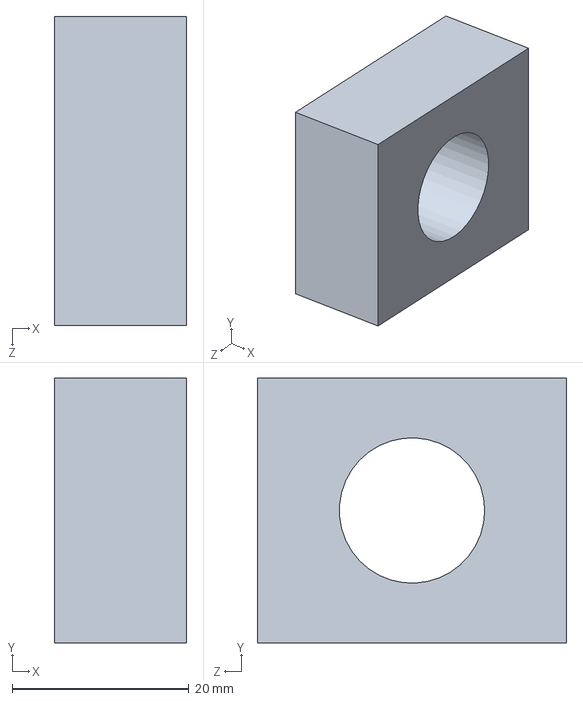
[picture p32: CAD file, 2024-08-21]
CAD/Bush.SLDPRT
15.0 x 30.0 x 35.0 mm

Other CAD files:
CAD/L1.IGS
CAD/Part3for.SLDPRT
CAD/L2.IGS
CAD/L.Co.SLDPRT
CAD/L.C.Afff.igs
CAD/L.C.A for.SLDPRT
CAD/L.C.A.stp
CAD/L.C.stp
CAD/L.Co1.SLDPRT
CAD/Part1.SLDPRT
CAD/L.C1.SLDPRT
CAD/L.C (2).stp
CAD/FF.IGS
CAD/L.C.A (2).CATPart
CAD/L.C.A (3).CATPart
CAD/L.C.A.CATPart
CAD/L.C.A.igs
CAD/L.C.Afff.CATPart
CAD/L.C.SLDPRT
CAD/L.Co.IGS
CAD/L.Co1.IGS

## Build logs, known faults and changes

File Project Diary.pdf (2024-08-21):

## Project Diary

September
Week 1 – Title Selected on the topic of Lower Control Arm.
Week 2 – Research done on the selected topic.
Week 3 – Searching and studying various research papers on the topic. Week 4 – Market Research to find the required Lower Control Arm. Week 5 – Market Survey and Purchasing of the Lower Control Arm.

October –
Week 6 – Inspecng and finding out the required dimensions of the Lower Control Arm. Week 7 – Taking out the measurements with the required tools and equipment.
Week 8 – Prepared Dra for the Lower Control Arm.
Week 9 – Started to prepare 3D Model of Lower Control Arm on Caa
Week 10 – Completed preparing model on Caa and Solidworks.

November – Ansys 1
Week 11 – Started to prepare Ansys on the Lower Control Arm. Week 12 – Learnt how to prepare a Ansys analysis.
Week 13 – Solved the problems regarding model in Ansys. Week 14 – Started applying condions on the model. Week 15 – Prepared Ansys for the exisng component.

December – UTM 1
Week 16 – Searched for a Universal Tesng Machine and its equipment in nearby locaon.
Week 17 – Found a Universal Tesng Machine and inspected how to mount the Lower Control Arm. Week 18 – Started preparing a mount on the Lower Control Arm.
Week 19 – Prepared the mounng for the Lower Control Arm.
Week 20 – Tesng done on the Universal Tesng Machine.

January – Ansys 2

Week 21 – Evaluated the results on the exisng component.
Week 22 – Started applying condion on exisng component in Ansys. Week 23 – Applied the condions on the exisng component.
Week 24 – Evaluated the results for the weight reducon.
Week 25 – Prepared the dimensions and the CAD for opmized component.

February – Fabricaon
Week 26 – Market Research to find the required fabricator. Week 27 – Taking out the dimensions on the model.
Week 28 – Preparing slot on the model.
Week 29 – Drilling the required hole on the prepared dimension on the model. Week 30 – Finishing on the work done on the model.

March – UTM 2
Week 31 – Started preparing a mount on the Lower Control Arm. Week 32 – Prepared the mounng for the Lower Control Arm. Week 33 – Tesng done on the Universal Tesng Machine.
Week 34 – Started preparing the report with the results. Week 35 – Prepared the report on the results.

April - Report
Week 36 – Started preparing the report on enre project. Week 37 – Collecng the required data for the report. Week 38 – Prepared the report on the data collected. Week 39 – Correcons done on the report.
Week 40 - Prepared the final report.
